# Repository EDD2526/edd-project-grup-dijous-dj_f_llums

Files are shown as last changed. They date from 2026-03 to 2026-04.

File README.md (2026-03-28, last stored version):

View this project on [CADLAB.io](https://cadlab.io/project/30200). 

# Projecte LLUMS

>**Autors:** 
>Martina Camprubí i Clara Rosaura

----------

## Objectiu

>PCB per control·lar les llums d'un vehicle a través d'un microcontrolador i comunicació CAN. 

## Diagrama de blocs

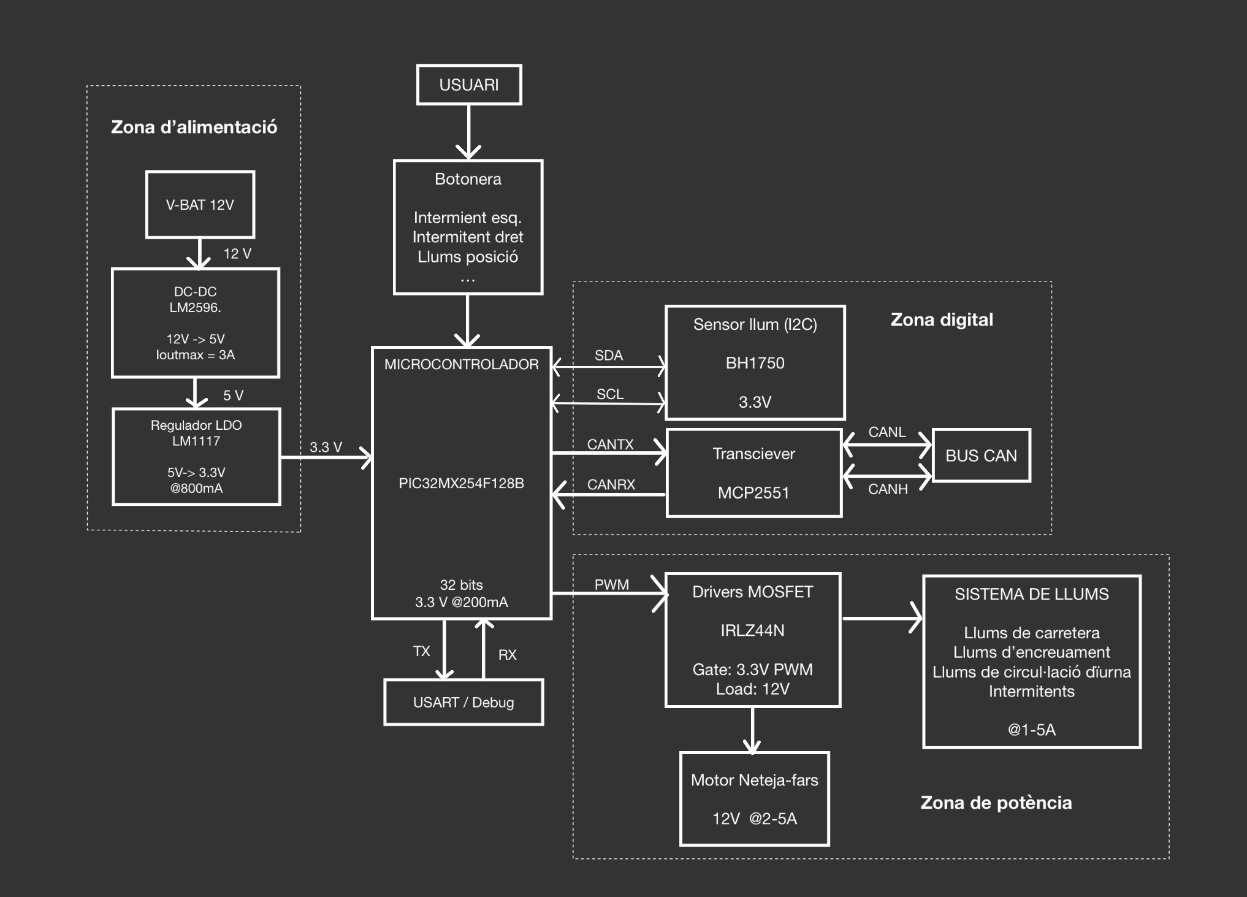
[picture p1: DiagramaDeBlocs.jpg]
Diagrama de blocs
>

### Descripció/funcionalitat de cada bloc

  * ZONA D'ALIMENTACIÓ:
	*V-BAT 12V: Entrada de tensió provinent de la bateria del vehicle.
	*DC-DC LM2596: Converteix els 12V a 5V.
	*LDO LM1117: Redueix els 5V a 3.3V per alimentar la lògica digital.
  * CONTROL PRINCIPAL:
	*MICROCONTROLADOR: Processa entrades i controla sortides del Sistema.
	*BOTONERA: Permet a l'usuari seleccionar les diferents funcions de llum i motor.
	*USART / DEBUG: Interfície per comunicació i depuració del Sistema.
  * ZONA DIGITAL:
	*SENSOR DE LLUM (BH1750): Mesura la llum ambiental via I2C per automatizar funcions.
	*TRANSCEIVER CAN (MCP2551): Adapta els senyals del micro al bus CAN del vehicle.
	*BUS CAN: Xarxa de comuniació amb altres sistemes del vehicle.
  * ZONA DE POTÈNCIA:
	*DRIVERS MOSFET (IRLZ44N): Actuen com interruptors per controlar càrregues de 12V.
	*SISTEMA DE LLUMS: Conjunt de llums del vehicle controlades electrònicament.
	*MOTOR NETEJA-FARS: Actuador de 12V per al sistema de neteja de fars.

-----------

## Requisits / Especificacions

  * Alimentació; 12V, regulada 5V
  * Microcontrolador PIC18xxxxxxxxx
  * ...

-----------

## Components

| Descripci&#243; | Ref | Package |Datasheet | Prove&#239;dor | Preu | Unitats |
| --- | --- | --- | --- | ---| --- | --- |
| Microcontrolador | PIC18F26Q83-I/SS | SOIC-28 |[Datasheet](https://www.mouser.es/datasheet/2/268/PIC18F27_47_57Q83_Preliminary_Data_Sheet_40002265B-2887591.pdf) | [Mouser](https://www.mouser.es/c/?q=PIC18F27Q83-I%2FSO)| 2,17&euro;| 1x |
| XTAL-Ressonador | CSTCR7M99G53-R0 | SMD |[Datasheet](https://www.mouser.es/datasheet/2/281/p16e-522700.pdf) | [Mouser](https://www.mouser.es/ProductDetail/Murata-Electronics/CSTCR7M99G53-R0?qs=Zd9RUO93%2Fo7cnwzsujIkpA%3D%3D)  | 0,27&euro; | 1x |

-----------

## Software

### Eines:

  * KiCad 9.0 o superior
  * 

### Configuraci&#243; :

  * 

### Funcionalitats:

  * 

-----------

## Historial de canvis

| Data | Autor | Branch | Versi&#243; | Descripci&#243; |
| --- | --- | --- | --- | --- |
|  28/03/2023 | mlopez | Master | initial commit | Primera versi&#243; d'esquem&#224;tic i selecci&#243; de components |

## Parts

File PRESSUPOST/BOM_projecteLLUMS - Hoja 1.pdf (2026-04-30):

Distribuidor | Dispositiu | Referència del fabricant | Referència del distribuidor | Qty (1 PCB) | Preu unitari | preu (10 PCB) | preu (50 PCB) | preu (1000 PCB) | preu (20.000 PCB) | Comentaris
RS | Condensador cerámico multicapa KEMET, 22 pF, 10 %, 50V dc, Montaje superficial, C0G dieléctrico C0805C220K5GACTU | | 205-3297 | 2 | 0.029€ (fins a 100u) 0.017€ (+1000u) | 2.90 | 2.90 | 34 | 680
RS | Condensador Panasonic serie FK, 680 μF, 20 %, 10V dc, Montaje superficial EEEFK1A681GL | | 262-1417P | 1 | 0,0413€ (fins a 100u) 0.023€ (+1.000u) 0.0148€ (+4000u) | 9.38 | 41.20 | 550 | 11000
RS | Condensador cerámico multicapa KEMET, 100 nF, 5 %, 100V dc, Montaje superficial, X7R dieléctrico C0805C104J1RACTU | | 205-3265P | 3 | 0,186€ (25-75u) 0.121€ (100-475u) 0.084€ (+2000u) | 9.30 | 18.15 | 252 | 5040
RS | Condensador cerámico multicapa KEMET, 100 nF, 5 %, 100V dc, Montaje superficial, X7R dieléctrico C0805C104J1RACTU | | 205-3265P | 3 | 0,186€ (25-75u) 0.121€ (100-475u) 0.084€ (+2000u) | 9.30 | 18.15 | 252 | 5040
RS | Condensador cerámico multicapa KEMET, 10 μF, ±10 %, 16V dc, Montaje superficial, X5R dieléctrico C0805C106K4PACTU | | 691-1161P | 2 | 0,129€ (10-40u) 0.121€ (100-475u) 0.098€ (+500u) | 2.58 | 11.30 | 196 | 3920
RS | LED Lite-On CHIP LED 0805, Blanco, Vf= 3.3 V, 130 °, Montaje superficial, encapsulado 2012 de 2 pines 1 LTW-170TK | | 703-1196P | 2 | 0,292€ (10-40u) 0.228€ (100-490u) 0.154€ (+1000u) | 5.84 | 22.80 | 308 | 6160
RS | Vishay Diodo, 1N5408-E3/54, Diodo rectificador, 3 A, 1 kV, DO-201AD, 2 pines 1N5408-E3/54 | | 628-9502 | 1 | 0,415€ (10-90u) 0.25€ (1000-2490u) 0.221€ (+2500u) | 4.15 | 20.75 | 250 | 4420
RS | ROHM Rectificador y diodo Schottky, RB160QS-40T18R, Diodo Schottky, 1.5 A, 40 V, SMD, 2 pines RB160QS-40T18R | | 235-2702P | 1 | 0.212€ (+25u) | 5.30 | 10.60 | 212 | 4240
RS | Conector de montaje en PCB Recta JST serie VH 2 contactos 1 filas, paso 3.96 mm, Orificio pasante Recubierto B2P-VH(LF)(SN) | | 172-4971 | 1 | 0.1€(1000u) | 100 | 100 | 100 | 2000 | La caixa dels components venen de 1000 en 1000, sense possibilitat de separació
RS | Cabezal de pines Recta RS PRO 3 contactos 1 filas, paso 2.54 mm, Orificio pasante Descubierto 304-02-995 | | 251-8092 | 1 | 0,209€ (25-475u) 0.174€ (500-1850u) 0.126€ (+15000u) | 5.225 | 10.45 | 174 | 2520 | Connector mascle 2.54mm
LCSC Electronics. | MAX MX126-5.0-02P-GN01-Cu-S-A | MX126-5.0-02P | C5188434 | 5 | 0.056€ (+10u) 0.045€(+100u) 0.04€(+300u) 0.032€(+1000u) 0.029€(+5000u) 0.027€(+10000u) | 0.65 | 5.28 | 167 | 3150 | Connector alimentació i llums
RS | Bloque de terminales PCB MKDS 3/ 3-5.08 HT BK Phoenix Contact de 3 contactos 1 filas, paso 5.08 mm, de color Negro 1985991 | | 855-2947 | 1 | 1.835€(50u) | 91,75 | 91,75 | 1835 | 36.700 | Connector motor
Farnell | Relé de Propósito General, Serie RYII, Potencia, SPDT, 5 VDC, 8 A 1-1956170-2 | | 1629032 | 1 | 4.14€(+1u) 3,690 €(+10u) 3,530€(+25u) 2,850€(+100u) 2,120€(+1120u) | 36,9 | 55,35 | 2.850 | 42.400
RS | AEC-Q200 Inductor de montaje superficial EPCOS, 33 μH, núcleo de Casquillo Sí Montaje superficial ±20 % bobinado, 3.35 A B82477P4333M000 | | 246-9835 | 1 | 1.52€ (10-49u) 1.32€ (+50u) | 15.20 | 66 | 1320 | 26400
RS | MOSFET, Tipo N-Canal Infineon, VDSS 55 V, ID 47 A, Mejora, TO-220 de 3 pines IRLZ44NPBF | | 919-4814 | 6 | 0,381€ (100-200u) 0.357€ (250-450u) 0.339€ (+1000u) | 38.10 | 107.10 | 2034 | 6780
RS | Resistencias de montaje en superficie Bourns, 10 kΩ, ±5 %, 0.125 W, Película gruesa, 0805 CR0805-JW-103ELF 150V, Serie CR0805-JW-103ELF | | 740-9072 | 13 | 0,012€ (50-450u) 0.009€ (+4000u) | 1.80 | 7.15 | 13 | 2340
RS | AEC-Q200 Resistencias de montaje en superficie Vishay, 680 Ω, ±1 %, 0.5 W, Película gruesa, 0805 Superficie CRCW0805680RFKEAHP | | 812-3628 | 2 | 0,093€ (25-225u) 0.032€ (1250-2475u) 0.026€ (+2500u) | 2.325 | 9.30 | 64 | 1040
RS | Resistencia Bourns, 120 Ω, 1 %, 0.5 W, Película gruesa, 0805 Montaje superficial CHP0805AFX-1200ELF 200V, Serie CHP CHP0805AFX-1200ELF | | 630-220 | 1 | 0,093€ (25-225u) 0.085€ (500-1980u) 0.064€ (+10000u) | 2.74 | 8.22 | 85 | 1280
RS | Resistencias de montaje en superficie KOA, 37.4 kΩ, ±0.1 %, 0.125 W, Película metálica, 0805 RN73R2ATTD3742B25 150V RN73R2ATTD3742B25 | | 205-0500 | 2 | 0,142€ (50-450u) 0.071€ (+1000u) | 7.1 | 14.20 | 142 | 2840
RS | Resistor fijado de montaje en superficie Yageo, 220 Ω, ±1 %, 0.125 W, Película gruesa, 0805 RC0805FR-07220RL 150V, Serie RC0805FR-07220RL | | 242-6935 | 5 | 0,01€ (100-900u) 0.008€ (1000-1900u) 0.007€ (+20000u) | 1 | 1 | 8 | 7
RS | Resistencias de montaje en superficie Bourns, 0 mΩ, ±5 %, 0.125 W, Película gruesa, 0805 CR0805-J/-000ELF 150V, Serie CR0805-J/-000ELF | | 740-9066 | 1 | 0,008€ (50-450u) 0.007 (1000-1950u) 0.064€ (+10000u) | 0.40 | 0.40 | 7 | 120
RS | Interruptor táctil Omron, contactos SPST Pulsador 9.5 mm, IP00, Orificio pasante 50 mA 6.1 mm B3F-1070 | | 686-6907 | 6 | 0,636 € (5-45u) 0,572 €(50-120u) 0,522 €(125-245u) 0,476 €(250-495u) 0,446 €(+500u) | 7,63€ | 34,32 | 535,20€ | 10.704

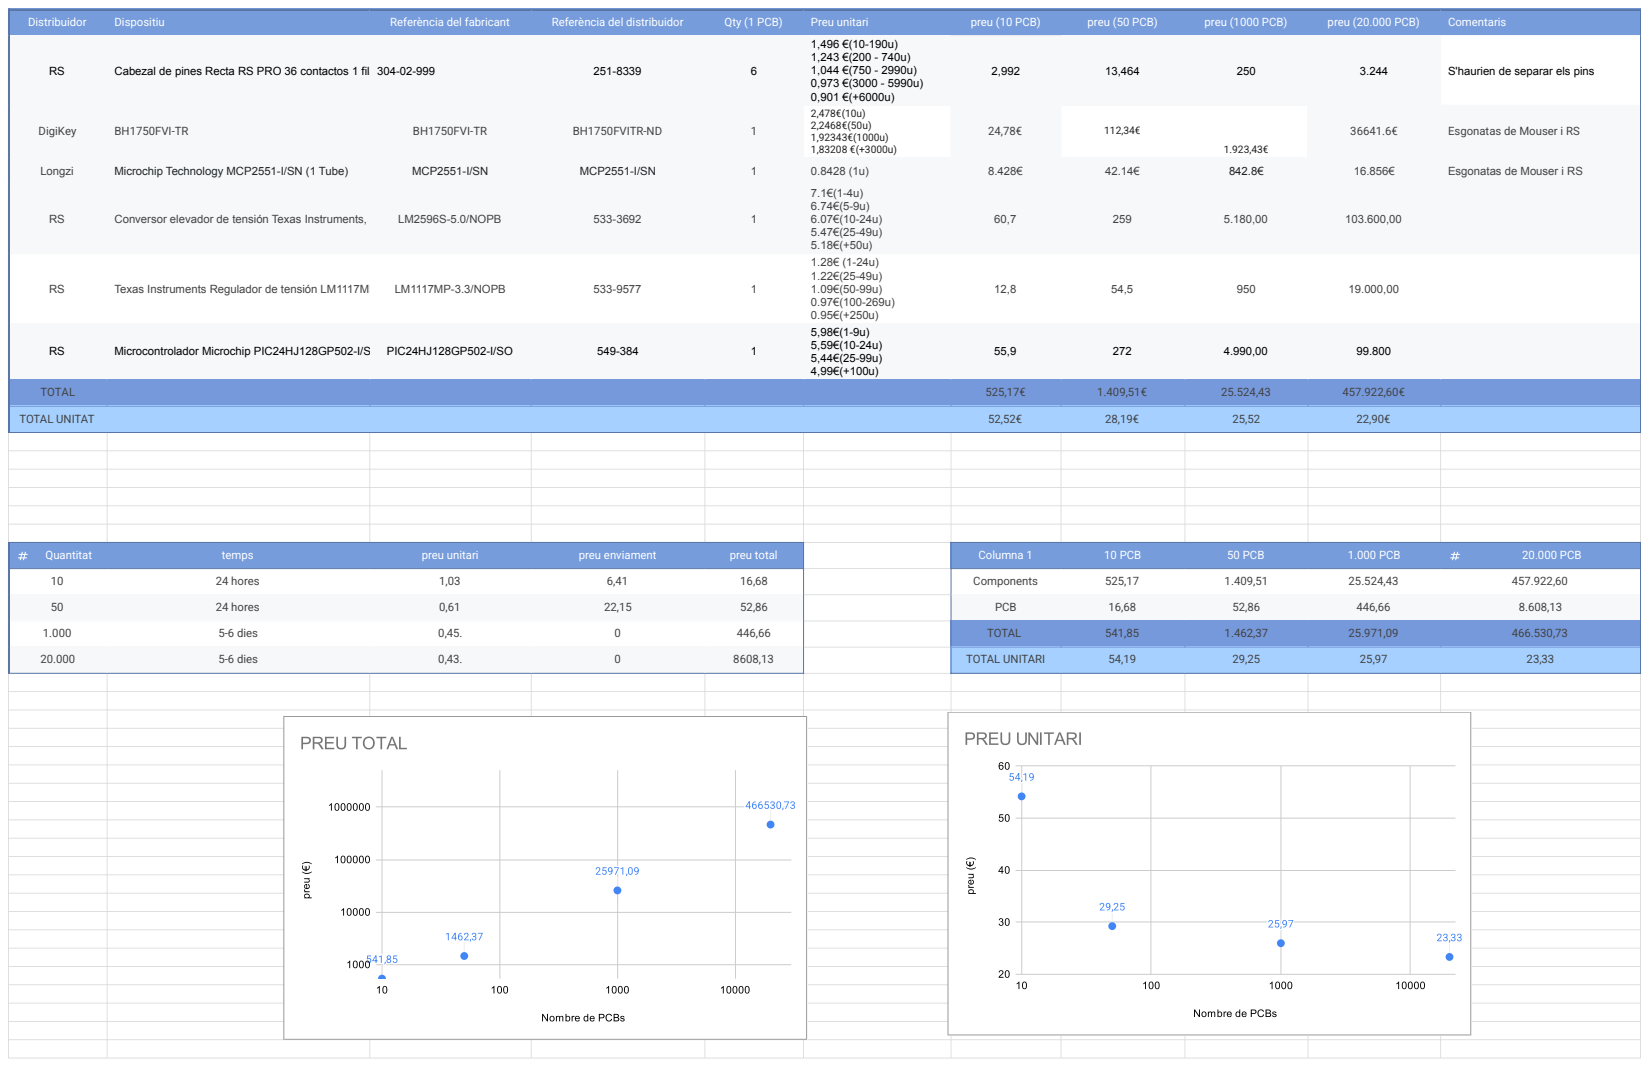
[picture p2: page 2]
Quantitat; temps; preu unitari; preu enviament; preu total; Columna 1; 10 PCB; 50 PCB; 1.000 PCB; 20.000 PCB; 24 hores; Components; PCB; 5-6 dies; TOTAL; TOTAL UNITARI; preu

Distribuidor | Dispositiu | Referència del fabricant | Referència del distribuidor | Qty (1 PCB) | Preu unitari | preu (10 PCB) | preu (50 PCB) | preu (1000 PCB) | preu (20.000 PCB) | Comentaris

RS | Cabezal de pines Recta RS PRO 36 contactos 1 filas, paso 2.54 mm, Orificio pasante Descubierto 304-02-999 | | 251-8339 | 6 | 1,496 €(10-190u) 1,243 €(200 - 740u) 1,044 €(750 - 2990u) 0,973 €(3000 - 5990u) 0,901 €(+6000u) | 2,992 | 13,464 | 250 | 3.244 | S'haurien de separar els pins

DigiKey | BH1750FVI-TR | BH1750FVI-TR | BH1750FVITR-ND | 1 | 2,478€(10u) 2,2468€(50u) 1,92343€(1000u) 1,83208 €(+3000u) | 24,78€ | 112,34€ | 1.923,43€ | 36641.6€ | Esgonatas de Mouser i RS

Longzi | Microchip Technology MCP2551-I/SN (1 Tube) | MCP2551-I/SN | MCP2551-I/SN | 1 | 0.8428 (1u) | 8.428€ | 42.14€ | 842.8€ | 16.856€ | Esgonatas de Mouser i RS

RS | Conversor elevador de tensión Texas Instruments, Salida 3.46V Montaje superficial, 3 A 1 LM2596S-5.0/NOPB | | 533-3692 | 1 | 7.1€(1-4u) 6.74€(5-9u) 6.07€(10-24u) 5.47€(25-49u) 5.18€(+50u) | 60,7 | 259 | 5.180,00 | 103.600,00

RS | Texas Instruments Regulador de tensión LM1117MP-3.3/NOPB 15V SOT-223, 4 pines LM1117MP-3.3/NOPB | | 533-9577 | 1 | 1.28€ (1-24u) 1.22€(25-49u) 1.09€(50-99u) 0.97€(100-269u) 0.95€(+250u) | 12,8 | 54,5 | 950 | 19.000,00

RS | Microcontrolador Microchip PIC24HJ128GP502-I/SO, núcleo PIC de 16 bit, 8 kB RAM, 128kB, 80 MHz, SOIC Flash de 28 pines PIC24HJ128GP502-I/SO | | 549-384 | 1 | 5,98€(1-9u) 5,59€(10-24u) 5,44€(25-99u) 4,99€(+100u) | 55,9 | 272 | 4.990,00 | 99.800

TOTAL | | | | | | 525,17€ | 1.409,51€ | 25.524,43 | 457.922,60€

TOTAL UNITAT | | | | | | 52,52€ | 28,19€ | 25,52 | 22,90€

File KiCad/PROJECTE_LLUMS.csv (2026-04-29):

Reference | Qty | Value | DNP | Exclude from BOM | Exclude from Board | Footprint | Datasheet
C1,C2 | 2 | 22pF |  |  |  | Capacitor_SMD:C_0805_2012Metric_Pad1.18x1.45mm_HandSolder | ~
C3 | 1 | 220uF |  |  |  | Capacitor_SMD:CP_Elec_6.3x5.4 | ~
C4 | 1 | 680uF |  |  |  | Capacitor_SMD:C_0805_2012Metric_Pad1.18x1.45mm_HandSolder | ~
C5,C9,C_out3 | 3 | 100nF |  |  |  | Capacitor_SMD:C_0805_2012Metric_Pad1.18x1.45mm_HandSolder | ~
C6,C7,C8 | 3 | 0.1uF |  |  |  | Capacitor_SMD:C_0805_2012Metric_Pad1.18x1.45mm_HandSolder | ~
C10,C11 | 2 | 10uF |  |  |  | Capacitor_SMD:C_0805_2012Metric_Pad1.18x1.45mm_HandSolder
D1,D2 | 2 | LED |  |  |  | LED_SMD:LED_0805_2012Metric_Pad1.15x1.40mm_HandSolder | ~
D7 | 1 | 1N5408 |  |  |  | Diode_THT:D_DO-201AD_P15.24mm_Horizontal | http://www.vishay.com/docs/88516/1n5400.pdf
D8 | 1 | SS34 |  |  |  | Diode_SMD:D_SMA | https://www.vishay.com/docs/88751/ss32.pdf
J1 | 1 | CONNECTOR_MOTOR |  |  |  | Connector_JST:JST_VH_B2P-VH_1x02_P3.96mm_Vertical | ~
J2,J5 | 2 | DE9_Pins_MountingHoles |  |  |  | Connector_Dsub:DSUB-9_Pins_Horizontal_P2.77x2.84mm_EdgePinOffset4.94mm_Housed_MountingHolesOffset4.94mm | ~
J3 | 1 | Conn_01x05 |  |  |  | Connector_PinHeader_2.54mm:PinHeader_1x05_P2.54mm_Vertical | ~
J4,J7,J8,J9,J10 | 5 | Conn_01x02_Pin |  |  |  | TerminalBlock:TerminalBlock_MaiXu_MX126-5.0-02P_1x02_P5.00mm | ~
J6 | 1 | Conn_01x02_Pin |  |  |  | TerminalBlock_Phoenix:TerminalBlock_Phoenix_MKDS-1,5-2-5.08_1x02_P5.08mm_Horizontal | ~
K1 | 1 | Fujitsu_FTR-LYAA005x |  |  |  | Relay_THT:Relay_1-Form-C_Schrack-RYII_RM3.2mm | https://www.fujitsu.com/sg/imagesgig5/ftr-ly.pdf
L1 | 1 | 33uH |  |  |  | Inductor_SMD:L_7.3x7.3_H4.5 | ~
Q2,Q3,Q4,Q5,Q6,Q7 | 6 | IRLZ44N |  |  |  | Package_TO_SOT_THT:TO-220-3_Vertical | http://www.irf.com/product-info/datasheets/data/irlz44n.pdf
R1,R7,R8,R9,R10,R11,R12 | 7 | 10K |  |  |  | Resistor_SMD:R_0805_2012Metric_Pad1.20x1.40mm_HandSolder | ~
R2,R3 | 2 | 680 |  |  |  | Resistor_SMD:R_0805_2012Metric_Pad1.20x1.40mm_HandSolder | ~
R13 | 1 | 12O |  |  |  | Resistor_SMD:R_0805_2012Metric_Pad1.20x1.40mm_HandSolder | ~
R14 | 1 | 10k |  |  |  | Resistor_SMD:R_0805_2012Metric_Pad1.20x1.40mm_HandSolder | ~
R19,R20 | 2 | 4.7k |  |  |  | Resistor_SMD:R_0805_2012Metric_Pad1.20x1.40mm_HandSolder | ~
R50 | 1 | 0 |  |  |  | Resistor_SMD:R_0805_2012Metric_Pad1.20x1.40mm_HandSolder | ~
SW1,SW2,SW3,SW4,SW5,SW6 | 6 | SW_Push |  |  |  | Button_Switch_THT:SW_PUSH_6mm | ~
TP_CANRX1,TP_CANTX1,TP_SCL1,TP_SDA1,TP_UART_RX1,TP_UART_TX1 | 6 | TestPoint |  |  |  | Connector_PinHeader_2.54mm:PinHeader_1x01_P2.54mm_Vertical | ~
U1 | 1 | BH1750FVI-TR |  |  |  | footprints:XDCR_BH1750FVI-TR
U2 | 1 | ~
U4 | 1 | MCP2551-I-SN |  |  |  | Package_SO:SOIC-8_3.9x4.9mm_P1.27mm | http://ww1.microchip.com/downloads/en/devicedoc/21667d.pdf
U5 | 1 | LM2596S-5 |  |  |  | Package_TO_SOT_SMD:TO-263-5_TabPin3 | http://www.ti.com/lit/ds/symlink/lm2596.pdf
U6 | 1 | LM1117MP-3.3 |  |  |  | Package_TO_SOT_SMD:SOT-223-3_TabPin2 | http://www.ti.com/lit/ds/symlink/lm1117.pdf
U7 | 1 | PIC24HJ128GP502 |  |  |  | projecte_llums:SOIC127P1030X265-28N
Y1 | 1 | 8MHz |  |  |  | Crystal:Crystal_SMD_3225-4Pin_3.2x2.5mm_HandSoldering | ~

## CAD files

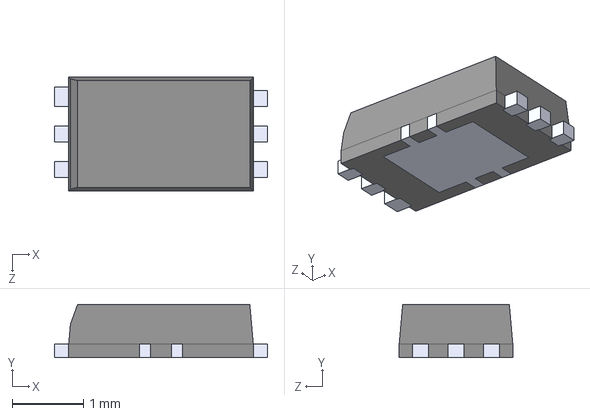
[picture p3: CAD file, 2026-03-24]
Symbols_footprints/BH1750FVI-TR/BH1750FVI-TR.step
3.00 x 0.75 x 1.60 mm

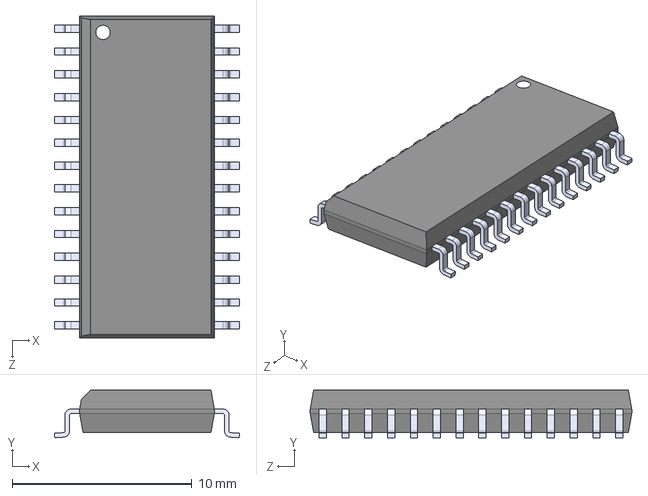
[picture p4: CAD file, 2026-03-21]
Symbols_footprints/PIC24HJ128GP502-I_SO/PIC24HJ128GP502-I_SO.step
10.3 x 2.65 x 17.9 mm

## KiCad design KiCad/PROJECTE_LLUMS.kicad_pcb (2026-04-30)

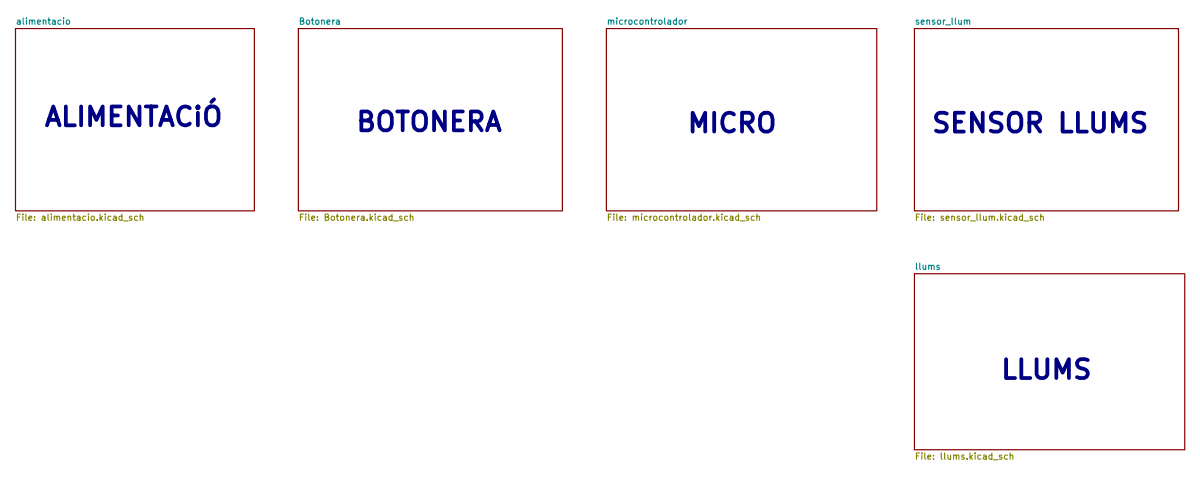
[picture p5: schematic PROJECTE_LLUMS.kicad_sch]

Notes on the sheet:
ALIMENTACiÓ
MICRO
LLUMS
BOTONERA
SENSOR LLUMS

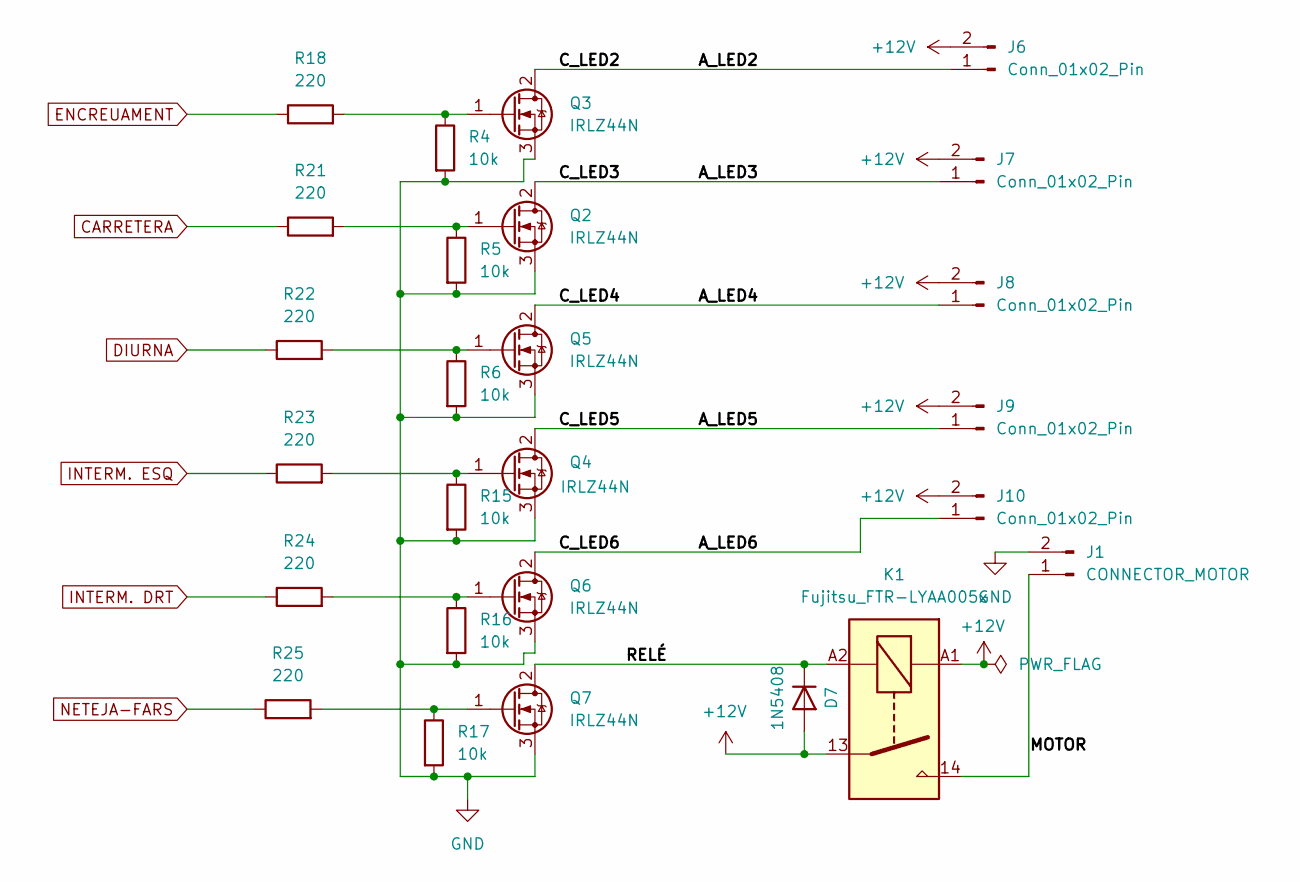
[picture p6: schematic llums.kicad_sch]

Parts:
D7: 1N5408; D_DO-201AD_P15.24mm_Horizontal
J1: CONNECTOR_MOTOR; JST_VH_B2P-VH_1x02_P3.96mm_Vertical
J6: Conn_01x02_Pin; TerminalBlock_Phoenix_MKDS-1,5-2-5.08_1x02_P5.08mm_Horizont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
J7, J8, J9, J10: Conn_01x02_Pin; TerminalBlock_MaiXu_MX126-5.0-02P_1x02_P5.00mm
K1: Fujitsu_FTR-LYAA005x; Relay_1-Form-C_Schrack-RYII_RM3.2mm
Q2, Q3, Q4, Q5, Q6, Q7: IRLZ44N; TO-220-3_Vertical
R4, R5, R6, R15, R16, R17: 10k; R_0805_2012Metric_Pad1.20x1.40mm_HandSolder
R18, R21, R22, R23, R24, R25: 220; R_0805_2012Metric_Pad1.20x1.40mm_HandSolder

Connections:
+12V: D7.2 (A), J6.2, J7.2, J8.2, J9.2, J10.2, K1.13, K1.A1
/llums/A_LED2: J6.1, Q3.2 (D)
/llums/A_LED3: J7.1, Q2.2 (D)
/llums/A_LED4: J8.1, Q5.2 (D)
/llums/A_LED5: J9.1, Q4.2 (D)
/llums/A_LED6: J10.1, Q6.2 (D)
/llums/MOTOR: J1.1, K1.14
/llums/RELÉ: D7.1 (K), K1.A2, Q7.2 (D)
CARRETERA: R21.1; also elsewhere on the board
DIURNA: R22.1; also elsewhere on the board
ENCREUAMENT: R18.1; also elsewhere on the board
GND: J1.2, Q2.3 (S), Q3.3 (S), Q4.3 (S), Q5.3 (S), Q6.3 (S), Q7.3 (S), R4.2, R5.2, R6.2, R15.2, R16.2, R17.2; also elsewhere on the board
INTERM. DRT: R24.1; also elsewhere on the board
INTERM. ESQ: R23.1; also elsewhere on the board
NETEJA-FARS: R25.1; also elsewhere on the board
unnamed: Q2.1 (G), R5.1, R21.2
unnamed: Q3.1 (G), R4.1, R18.2
unnamed: Q4.1 (G), R15.1, R23.2
unnamed: Q5.1 (G), R6.1, R22.2
unnamed: Q6.1 (G), R16.1, R24.2
unnamed: Q7.1 (G), R17.1, R25.2

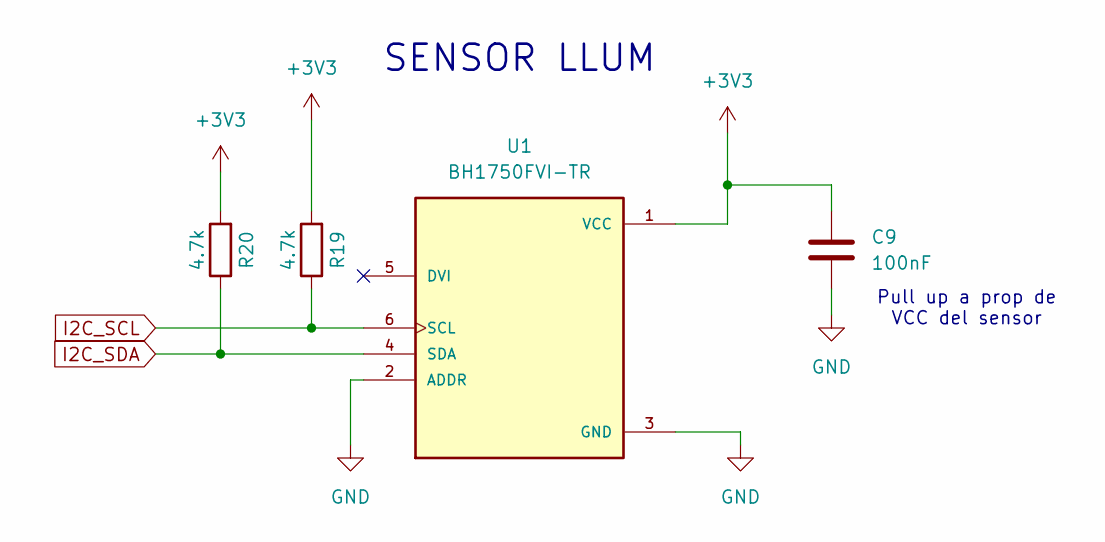
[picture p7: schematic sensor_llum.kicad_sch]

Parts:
C9: 100nF; C_0805_2012Metric_Pad1.18x1.45mm_HandSolder
R19, R20: 4.7k; R_0805_2012Metric_Pad1.20x1.40mm_HandSolder
U1: BH1750FVI-TR; XDCR_BH1750FVI-TR; PARTREV D

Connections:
+3V3: C9.1, R19.2, R20.2, U1.1 (VCC); also elsewhere on the board
GND: C9.2, U1.2 (ADDR), U1.3 (GND); also elsewhere on the board
I2C_SCL: R19.1, U1.6 (SCL); also elsewhere on the board
I2C_SDA: R20.1, U1.4 (SDA); also elsewhere on the board

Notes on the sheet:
SENSOR LLUM
Pull up a prop de VCC del sensor

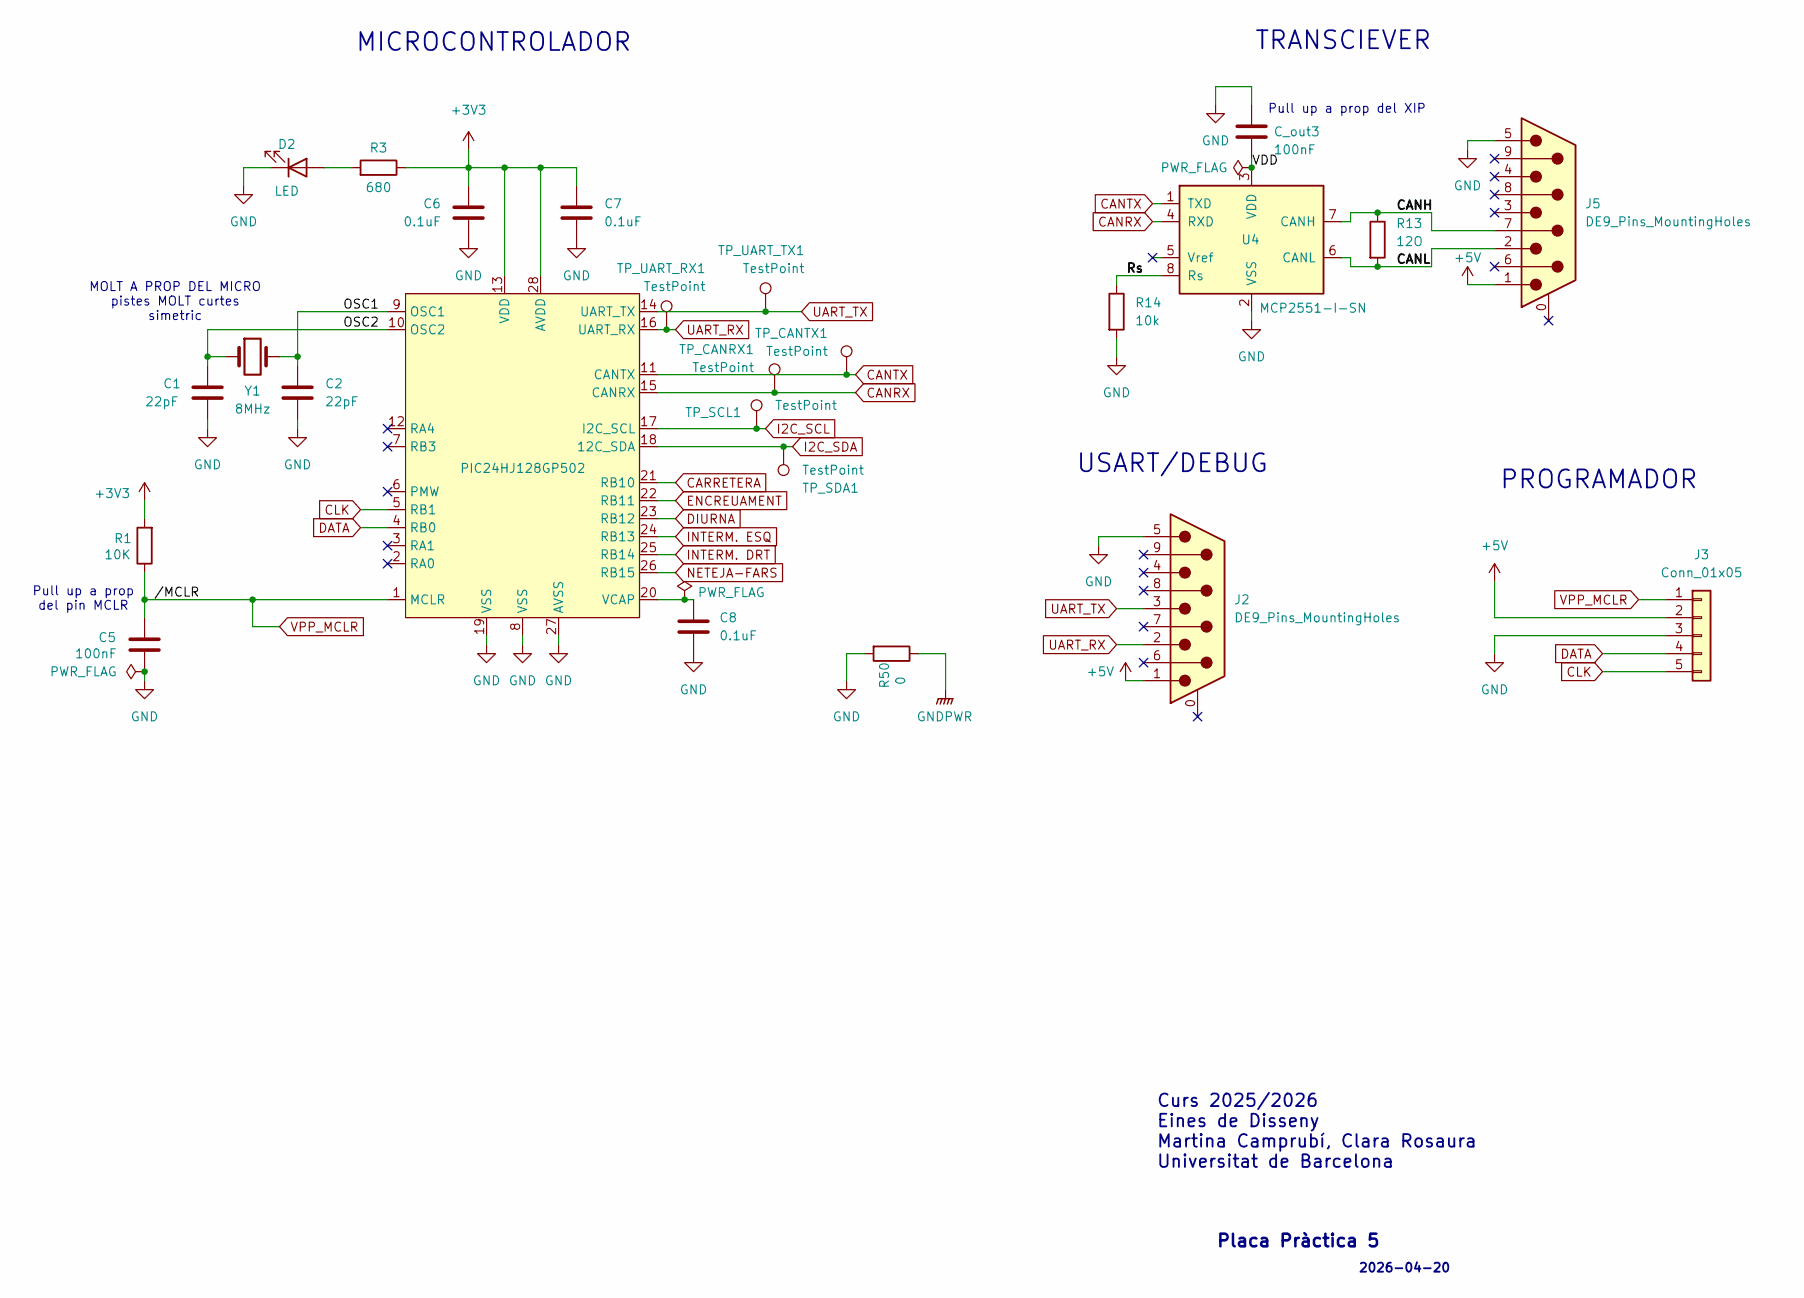
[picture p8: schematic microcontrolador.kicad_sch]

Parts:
C1, C2: 22pF; C_0805_2012Metric_Pad1.18x1.45mm_HandSolder
C5: 100nF; C_0805_2012Metric_Pad1.18x1.45mm_HandSolder
C6, C7, C8: 0.1uF; C_0805_2012Metric_Pad1.18x1.45mm_HandSolder
C_out3: 100nF; C_0805_2012Metric_Pad1.18x1.45mm_HandSolder
D2: LED; LED_0805_2012Metric_Pad1.15x1.40mm_HandSolder
J2, J5: DE9_Pins_MountingHoles; DSUB-9_Pins_Horizontal_P2.77x2.84mm_EdgePinOffset4.94mm_Hou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
J3: Conn_01x05; PinHeader_1x05_P2.54mm_Vertical
R1: 10K; R_0805_2012Metric_Pad1.20x1.40mm_HandSolder
R3: 680; R_0805_2012Metric_Pad1.20x1.40mm_HandSolder
R13: 12O; R_0805_2012Metric_Pad1.20x1.40mm_HandSolder
R14: 10k; R_0805_2012Metric_Pad1.20x1.40mm_HandSolder
R50: 0; R_0805_2012Metric_Pad1.20x1.40mm_HandSolder
TP_CANRX1: TestPoint; PinHeader_1x01_P2.54mm_Vertical
TP_CANTX1: TestPoint; PinHeader_1x01_P2.54mm_Vertical
TP_SCL1: TestPoint; PinHeader_1x01_P2.54mm_Vertical
TP_SDA1: TestPoint; PinHeader_1x01_P2.54mm_Vertical
TP_UART_RX1: TestPoint; PinHeader_1x01_P2.54mm_Vertical
TP_UART_TX1: TestPoint; PinHeader_1x01_P2.54mm_Vertical
U2: (no value)
U4: MCP2551-I-SN; SOIC-8_3.9x4.9mm_P1.27mm
U7: PIC24HJ128GP502; SOIC127P1030X265-28N
Y1: 8MHz; Crystal_SMD_3225-4Pin_3.2x2.5mm_HandSoldering

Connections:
+3V3: C6.1, C7.1, R1.2, R3.1, U7.13 (VDD), U7.28 (AVDD); also elsewhere on the board
+5V: J2.1, J3.2, J5.1; also elsewhere on the board
/microcontrolador/CANH: J5.7, R13.1, U4.7 (CANH)
/microcontrolador/CANL: J5.2, R13.2, U4.6 (CANL)
/microcontrolador/OSC1: C2.1, U7.9 (OSC1), Y1.2
/microcontrolador/OSC2: C1.1, U7.10 (OSC2), Y1.1
/microcontrolador/Rs: R14.1, U4.8 (Rs)
/microcontrolador/VDD: C_out3.2, U4.3 (VDD)
CANRX: TP_CANRX1.1, U4.4 (RXD), U7.15 (CANRX)
CANTX: TP_CANTX1.1, U4.1 (TXD), U7.11 (CANTX)
CARRETERA: U7.21 (RB10); also elsewhere on the board
CLK: J3.5, U7.5 (RB1)
DATA: J3.4, U7.4 (RB0)
DIURNA: U7.23 (RB12); also elsewhere on the board
ENCREUAMENT: U7.22 (RB11); also elsewhere on the board
GND: C1.2, C2.2, C5.2, C6.2, C7.2, C8.2, C_out3.1, D2.1 (K), J2.5, J3.3, J5.5, R14.2, R50.2, U4.2 (VSS), U7.8 (VSS), U7.19 (VSS), U7.27 (AVSS); also elsewhere on the board
GNDPWR: R50.1; also elsewhere on the board
I2C_SCL: TP_SCL1.1, U7.17 (I2C_SCL); also elsewhere on the board
I2C_SDA: TP_SDA1.1, U7.18 (12C_SDA); also elsewhere on the board
INTERM. DRT: U7.25 (RB14); also elsewhere on the board
INTERM. ESQ: U7.24 (RB13); also elsewhere on the board
NETEJA-FARS: U7.26 (RB15); also elsewhere on the board
unnamed: D2.2 (A), R3.2
unnamed: C8.1, U7.20 (VCAP)
UART_RX: J2.2, TP_UART_RX1.1, U7.16 (UART_RX)
UART_TX: J2.3, TP_UART_TX1.1, U7.14 (UART_TX)
VPP_MCLR: C5.1, J3.1, R1.1, U7.1 (MCLR)

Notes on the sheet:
TRANSCIEVER
USART/DEBUG
PROGRAMADOR
2026-04-20
MOLT A PROP DEL MICRO pistes MOLT curtes simetric
Curs 2025/2026 Eines de Disseny Martina Camprubí, Clara Rosaura Universitat de Barcelona
MICROCONTROLADOR
Pull up a prop del pin MCLR
Pull up a prop del XIP
Placa Pràctica 5

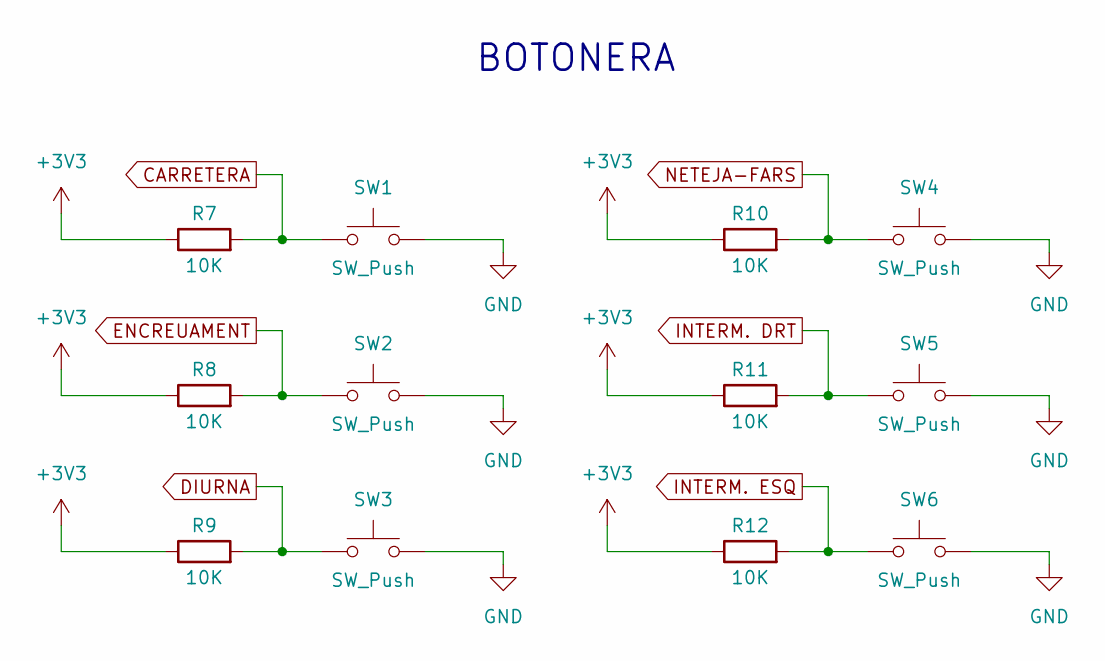
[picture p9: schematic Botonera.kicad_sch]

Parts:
R7, R8, R9, R10, R11, R12: 10K; R_0805_2012Metric_Pad1.20x1.40mm_HandSolder
SW1, SW2, SW3, SW4, SW5, SW6: SW_Push; SW_PUSH_6mm

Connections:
+3V3: R7.1, R8.1, R9.1, R10.1, R11.1, R12.1; also elsewhere on the board
CARRETERA: R7.2, SW1.1; also elsewhere on the board
DIURNA: R9.2, SW3.1; also elsewhere on the board
ENCREUAMENT: R8.2, SW2.1; also elsewhere on the board
INTERM. DRT: R11.2, SW5.1; also elsewhere on the board
INTERM. ESQ: R12.2, SW6.1; also elsewhere on the board
NETEJA-FARS: R10.2, SW4.1; also elsewhere on the board
unnamed: SW1.2, SW2.2, SW3.2, SW4.2, SW5.2, SW6.2

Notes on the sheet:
BOTONERA

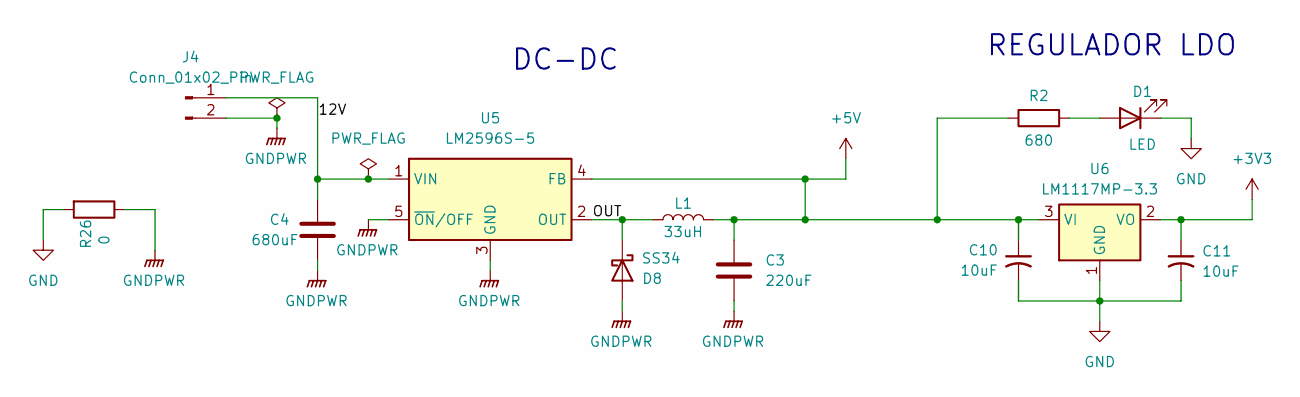
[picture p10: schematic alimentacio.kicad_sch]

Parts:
C3: 220uF; CP_Elec_6.3x5.4
C4: 680uF; C_0805_2012Metric_Pad1.18x1.45mm_HandSolder
C10, C11: 10uF; C_0805_2012Metric_Pad1.18x1.45mm_HandSolder
D1: LED; LED_0805_2012Metric_Pad1.15x1.40mm_HandSolder
D8: SS34; D_SMA
J4: Conn_01x02_Pin; TerminalBlock_MaiXu_MX126-5.0-02P_1x02_P5.00mm
L1: 33uH; L_7.3x7.3_H4.5
R2: 680; R_0805_2012Metric_Pad1.20x1.40mm_HandSolder
R26: 0; R_0805_2012Metric_Pad1.20x1.40mm_HandSolder
U5: LM2596S-5; TO-263-5_TabPin3
U6: LM1117MP-3.3; SOT-223-3_TabPin2

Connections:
+3V3: C11.1, U6.2 (VO); also elsewhere on the board
+5V: C3.1, C10.1, L1.2, R2.1, U5.4 (FB), U6.3 (VI); also elsewhere on the board
/alimentacio/12V: C4.1, J4.1, U5.1 (VIN)
/alimentacio/OUT: D8.1 (K), L1.1, U5.2 (OUT)
GND: C10.2, C11.2, D1.1 (K), R26.2, U6.1 (GND); also elsewhere on the board
GNDPWR: C3.2, C4.2, D8.2 (A), J4.2, R26.1, U5.3 (GND), U5.5 (~ON/OFF); also elsewhere on the board
unnamed: D1.2 (A), R2.2

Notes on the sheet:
DC-DC
REGULADOR LDO

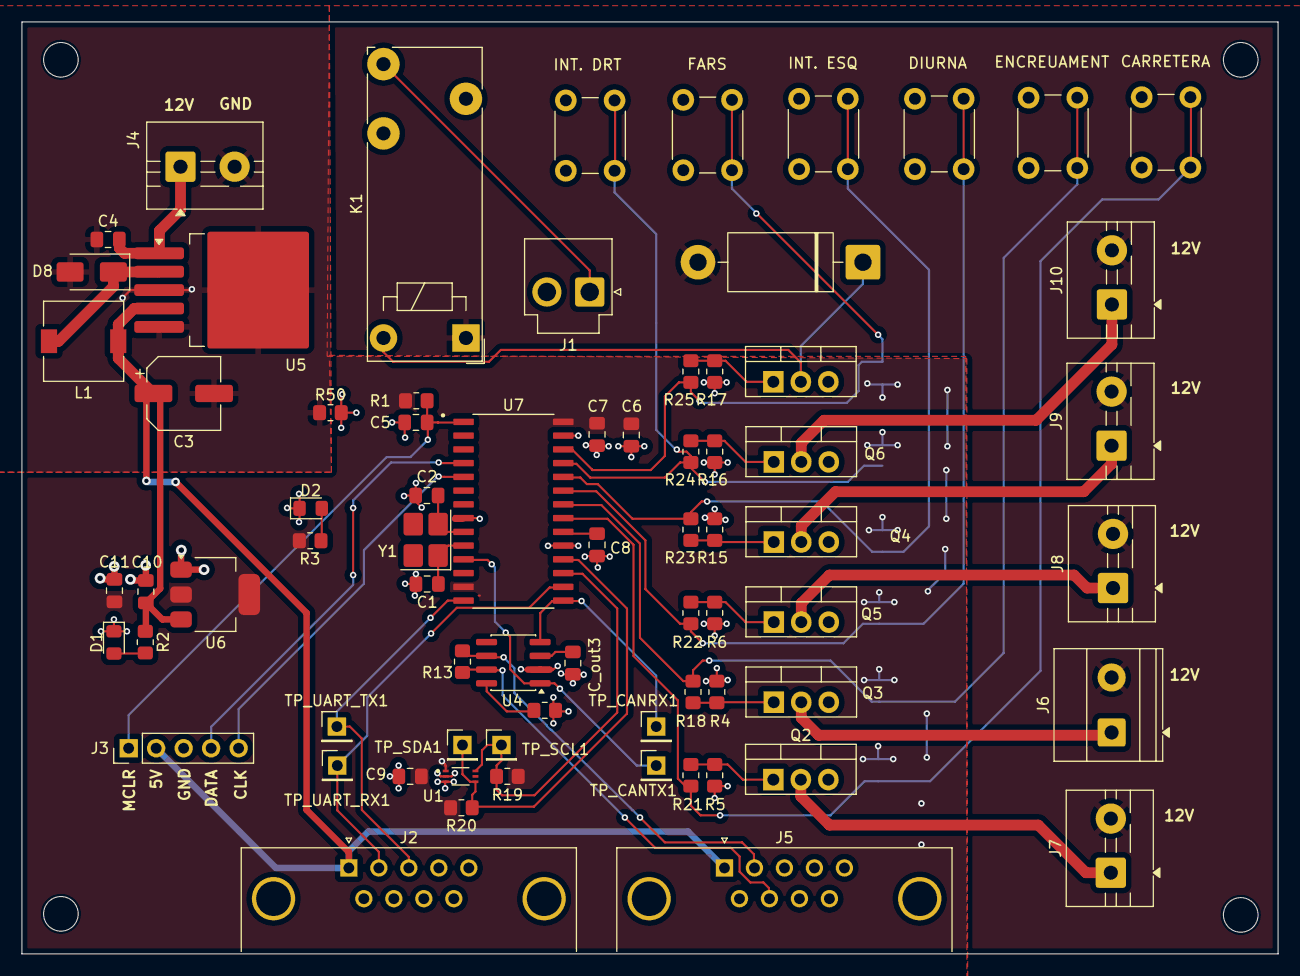
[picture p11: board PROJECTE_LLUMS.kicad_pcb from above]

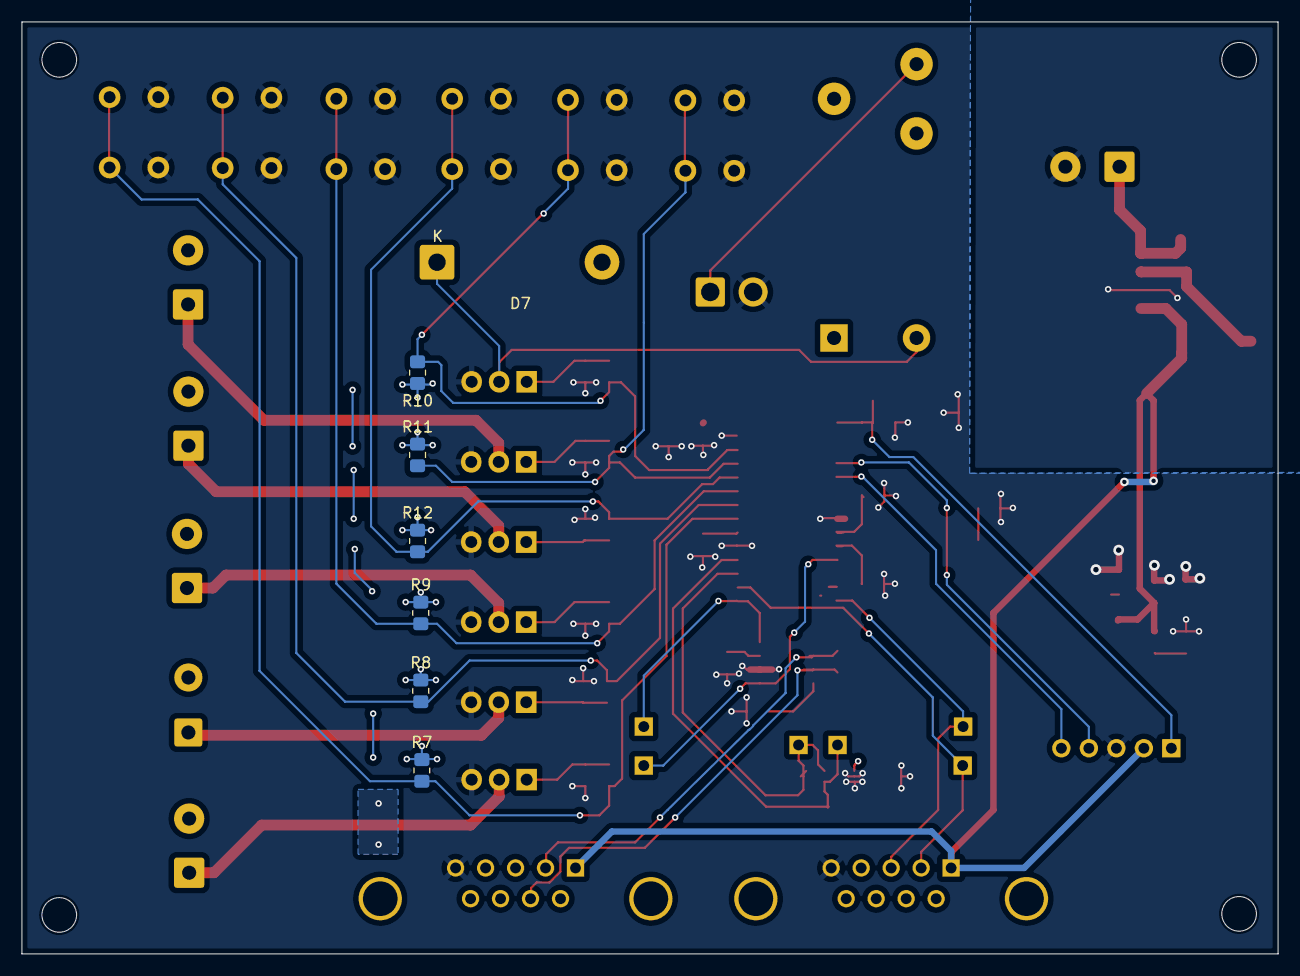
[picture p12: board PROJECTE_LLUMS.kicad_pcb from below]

Board: 2 copper layers, 116.1 x 86.1 mm, 78 parts (6 on the bottom side), 44 nets.

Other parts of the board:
CARRETERA: SW_Push; SW_PUSH_6mm
DIURNA: SW_Push; SW_PUSH_6mm
ENCREUAMENT: SW_Push; SW_PUSH_6mm
FARS: SW_Push; SW_PUSH_6mm
INT. DRT, INT. ESQ: SW_Push; SW_PUSH_6mm

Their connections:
CARRETERA: CARRETERA.1; also elsewhere on the board
DIURNA: DIURNA.1; also elsewhere on the board
ENCREUAMENT: ENCREUAMENT.1; also elsewhere on the board
GND: CARRETERA.2, DIURNA.2, ENCREUAMENT.2, FARS.2, INT. DRT.2, INT. ESQ.2; also elsewhere on the board
INTERM. DRT: INT. DRT.1; also elsewhere on the board
INTERM. ESQ: INT. ESQ.1; also elsewhere on the board
NETEJA-FARS: FARS.1; also elsewhere on the board

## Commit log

2026-03-12 canvi de nom
2026-03-12 kitkat creat
    [PROJECTE_LLUMS.kicad_pcb]
2026-03-17 DC-DC i transciever
    [PROJECTE_LLUMS.kicad_sch]
2026-03-17 part llums
    [PROJECTE_LLUMS.kicad_sch]
2026-03-19 llums bé pagina nova
    [PROJECTE_LLUMS.kicad_sch, untitled.kicad_sch]
2026-03-19 llums bé amb les etiquetes bé
    [PROJECTE_LLUMS.kicad_sch, untitled.kicad_sch]
2026-03-19 esquemàtic amb totes les cel·les
    [Botonera.kicad_sch, Debug.kicad_sch, PROJECTE_LLUMS.kicad_sch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]
2026-03-21 he afegit tot lo del old al new
    [PIC24HJ128GP502-I_SO.step, llums.kicad_sch]
2026-03-21 he canviat el micro
    [Botonera.kicad_sch, Debug.kicad_sch, alimentacio.kicad_sch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]
2026-03-24 ERC i footprints
    [BH1750FVI-TR.step, Botonera.kicad_sch, Debug.kicad_sch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]
2026-03-24 placement (falten LEDs)
    [PROJECTE_LLUMS.kicad_pcb, microcontrolador.kicad_sch, sensor_llum.kicad_sch]
2026-03-25 correcció d'errors CADLAB, falten els de llums i un parell que no entenc
    [Debug.kicad_sch, PROJECTE_LLUMS.kicad_pcb, PROJECTE_LLUMS.kicad_sch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]
2026-03-25 Esquemàtic acabat amb llums incorporades
    [PROJECTE_LLUMS.kicad_pcb]
2026-03-26 errors cadlab
    [alimentacio.kicad_sch, sensor_llum.kicad_sch, transciever.kicad_sch]
2026-03-26 errors pcb
    [PROJECTE_LLUMS.kicad_pcb, alimentacio.kicad_sch, sensor_llum.kicad_sch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]
2026-03-26 relé fet
    [llums.kicad_sch]
2026-03-28 alguns errors de CADLAB i he canivat d'ordre els LEDs i els drivers a la PCB.
    [Botonera.kicad_sch, PROJECTE_LLUMS.kicad_pcb, alimentacio.kicad_sch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]
2026-04-01 modificacions cadlab
    [PROJECTE_LLUMS.kicad_pcb, alimentacio.kicad_sch, microcontrolador.kicad_sch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]
2026-04-07 he esborrat els esquemàtics del transciever i USART
    [PROJECTE_LLUMS.kicad_sch]
2026-04-09 Relé??
    [PROJECTE_LLUMS.kicad_pcb, llums.kicad_sch]
2026-04-09 correccions Manel
    [PROJECTE_LLUMS.kicad_pcb, llums.kicad_sch, microcontrolador.kicad_sch]
2026-04-13 algo de routing
    [PROJECTE_LLUMS.kicad_pcb, microcontrolador.kicad_sch]
2026-04-15 Connectors amb huellas
    [PROJECTE_LLUMS.kicad_pcb, llums.kicad_sch]
2026-04-16 presentació
    [PROJECTE_LLUMS.kicad_pcb]
2026-04-16 routing def
    [PROJECTE_LLUMS.kicad_pcb]
2026-04-17 test points schematic
    [alimentacio.kicad_sch, microcontrolador.kicad_sch]
2026-04-20 test points ALIMENTACIO, UART, CAN
    [PROJECTE_LLUMS.kicad_pcb]
2026-04-20 errors de connexio no solucionats
    [PROJECTE_LLUMS.kicad_pcb]
2026-04-27 errors 3V3
    [PROJECTE_LLUMS.kicad_pcb]
2026-04-29 LLums finals amb resistències afegides
    [PROJECTE_LLUMS.kicad_pcb, llums.kicad_sch]
2026-04-29 errors finals
    [PROJECTE_LLUMS.csv, PROJECTE_LLUMS.kicad_pcb]
2026-04-30 push final (?)
    [PROJECTE_LLUMS.kicad_pcb, alimentacio.kicad_sch, microcontrolador.kicad_sch]
2026-04-30 PRESENTACIÓ FINAL
    [PROJECTE_LLUMS.kicad_pcb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]
